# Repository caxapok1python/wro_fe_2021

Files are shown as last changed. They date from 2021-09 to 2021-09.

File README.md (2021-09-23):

# World Robotic Olympiad 2021 Future Engineers

## Our YouTube Video
    https://youtu.be/UyoNl7fKj5E

## Introduction

The pandemic has accelerated the introduction of digital technologies in all spheres of life. 41% of company executives from 45 countries are preparing to work in a new post-crisis reality, investing in accelerating business automation.

Sustainable development of companies even before the pandemic was associated with digital technologies. Automation of transport gives many advantages, but it is also important that the introduction of machine labour reduces risks. Some of them are shortages of workers, low attractiveness of labour in the industry. These circumstances necessitate the use of labour-saving technologies: digital, intellectual and robotic. Basically, these technologies are represented by robotics, one of the most important functions of which is intellectual, it is to quickly obtain information, data on processes performed and products to improve the efficiency of decision-making and implementation of management decisions in autonomous movement. When introducing robotics in logistics organisations, it is necessary to take into account the regional characteristics and specifics of specific sectors of transportation. Regional features of robotics may be related to the peculiarities of the region's development. These features include the level and conditions of socio-economic development of the region, infrastructure development, demographic trends, competitiveness of the transport sector to attract labour in comparison with other industries, etc. Industry features that require robotisation may be related to the need to perform monotonous repetitive processes, the presence of heavy, dangerous and harmful activities. An important condition for robotisation of processes in the field of transportation is the possibility of compiling certain algorithms that underlie the functioning of robotics.

##### Based on the above facts, the following tasks of robotics in the field of transportation can be distinguished:

- Monitoring and forecasting;

- Reducing the cost of transportation;

- Improving logistics security;

- Solving personnel problems;

- Reducing the costs of employees' bad faith;

- Expanding the possibilities of using equipment - robots can be all-weather and work at any time of the day.

``Kinematic scheme``

``Calculation part``

>3.1 Engine calculation
    
1) Motor torque is the force with which it acts on the rotating axle. In order for the robot to move, it is necessary that this force exceeds the weight of the robot (expressed in N/m).

When travelling in a straight line at a distance of 1 m, calculate the acceleration required to achieve a speed of 1 m/s.

    V^2 = v_0^2+2ad

Where is the distance travelled by the robot - its initial speed (start from the place, so ),

    A = (v^2-v_0^2)/2d

Where is the speed of the robot, its acceleration.

Substitute the values adopted in our model, we'll get

    A = (1^2-0)/2=0.5 m/c^2 - acceleration required to achieve a speed of 1 m/s

The torque that is necessary to move the robot and obtain the acceleration necessary to achieve maximum speed is calculated as follows:

When - moment of inertia and - angular acceleration, we get

    M = mrag/2=(8*9.8*0.13*10)/2=51 
        (mN*m)=0.52 (kg*cm)

Here m/s2 - acceleration of free fall (round it to 10), - radius of the wheel, - mass of the entire robot

To convert the value expressed in Nm to kg·cm, it should be taken into account that 1H = 0.102 kg and 1m = 100 cm. Therefore, 50 mN·m = 50 · 0.102 : 1000 * 100 = 0.51 kg · cm.

2) To calculate the maximum power of the engines, we will need a speed that is expressed in revolutions per minute

#####
    V=60ω/2πr (rpm)
#####
    V=(60*1)/(2π*0.13)=73.46 (rpm)

Motor power is proportional to torque and speed, substituting formulas for torque and frequency, we get:

    P=M*v=(8*9.8*0.13*0.5)/(2*0.13)=19.6 (W)

We got the total power for all engines, in our case the engines are two, so we need to divide the result by two.

For our two-wheeled robot, using a gear ratio equal to 10, the characteristics of the installed engines should be as follows:

**Speed** - 2000 rpm.

**Torque** - 60 mN*m

**Electric power** - 50 W

>3.2 Servo drive calculation

The robot on the turn of the front axle uses micro servo 9g sg 90 servo drives.

The torque on the shaft of this drive is 1.6 kg cm.

The maximum load of the inverted wheel is 1-1.3 kg.

When the servo drive is located on the axis of rotation of the swivel fist with a stop of the drive nozzle to the upper fist, we create a moment of force that allows you to keep the wheel in the required angle.

    M=[r *F ]

Where is M torque?

    F - power
    R - radius

Using this formula, we can find the power that the servo drive can withstand.

Given:

    M=1.6 (kg*cm) = 0.16 (H*m)
#####
    R=0.025( m)
#####
    F=M/r=0.16/0.025=6.4 (H)

Conclusion: Such power is enough for our task, as the servo acts through the lever, not directly.

>3.3 Screw calculation

-   Information system.

>>4.1 Electronic components 
>####4.1.1 selection of engine control driver.
>Dual L298N driver - made on the basis of the L298N chip with low internal resistance, PWM control capability and output current up to 5 A, which is a suitable solution for a project with high current consumption. The L298N driver is compatible with the entire Arduino line as well as with any other microcontrollers.

**Characteristics:**

- logic voltage 5 Volts;

- engine operating voltage from 7.2 to 20 Volts DC;

- operating output current to the channel up to 68A (start mode);

**Size:** 4.5*4.1 cm.

The motor paired driver works debugged, as the operating current is enough for the motor, which at its peak consumes 2A at 12V.

>4.1.2 Battery calculation

**Single battery:**

Formulas that determine the relationship between the current that the battery gives to the load, its capacity and the relative discharge rate:

    I_bat = C_rate*C_bat
#####
    I_bat - current in amperes given to the load by one battery;
    
**C_bat** - nominal battery capacity in ampere hours (means the product of amperes per watch), which is usually labelled on the battery;

C_rate is the relative discharge rate of the battery, defined as the discharge current divided by the theoretical current that the battery can give out within one hour and its capacity will be fully consumed.

**I_bat** = 30 A;

**C_bat** = 3000 mAh;

Where does **C_rate** = 10 seconds come from;

Operating time t and relative discharge rate of the C_rate battery are bound by an inverse proportional dependence:

    t=1/C_rate

Let's note that this is a theoretical time of work. Due to a variety of external factors, real operating time will be about 30% less than calculated according to this formula. It should also be noted that the permissible discharge depth of the battery further limits its operating time.

The watt-hour energy stored in the battery is calculated by the formula:

    E_bat=V_bat C_bat^

**Here:**

**E_bat** - nominal energy stored in the battery in watt hours,

**V_bat** - rated battery voltage in volts

**C_bat** - nominal battery capacity in ampere hours (Ah)

**V_bat** = 4.2 B;

**E_bat** = 12.6 Wh;

The energy in joules (watt seconds, Wt-s) is calculated by the formula

    E_(bat,joul) = 3600*E_(bat,Wh);
#####
    E_(bat,joul) = 45.36 kJ;

It is known that at a current of one ampere, a charge of one pendant passes through the cross section of the conductor in one second. Therefore, the battery charge is determined from the expression Q = I · t, taking into account the known battery capacity in ampere hours, which determines the current given by the battery to the load for 3600 seconds:

    Q_bat = 3600<OPUS-CC>*C_BAT_

**Q_bat** - battery charge in pendants (K)

Cbat is the nominal capacity of the battery in ampere hours.

**Q_bat** = 108 kCl;

**Battery pack**

The rated voltage of the battery pack in volts is determined by the formula:

V_bank=V_bat*N_s

**Here:**

**Vbat** - rated voltage of the battery in volts,

**Vbank** - rated voltage of the battery pack in volts

**Ns** - number of batteries in one of several groups of serially connected batteries;

**Ns** = 4 pcs.

**Vbank** = 16.8 V;

Battery capacity in ampere hours, **Cbank** is determined by the formula:

    C_bank=C_bat*N_p

**C_bank** = 12 Ah;

The nominal energy in Ebank watt hours stored in the battery pack is determined by the formula:

    E_bank = E_bat *N_p*N_s_

**Np** - the number of groups of serially connected batteries connected in parallel

**Np** = 4 pcs.

**E_bank** = 201.6 Wh

Joule energy is calculated by the formula:

    E_(bank,joul) = 3600*E_(bank,Wh)

Here Ebank, Wh is the nominal energy of the battery pack in watt hours.

    E_(bank,joul) = 725.76 kJ;

The charge in the pendants of the Qbank battery pack is defined as the sum of the charges of all batteries in the unit:

    Q_bank = Q_bat*N_p *N_s

**Q_bank**=1 728 kCl

The discharge current of the Ibank battery pack is calculated by the formula:

    I_bank = I_bat*N_p

**I_bank** = 120 A

The operating time of the tbank battery pack is determined by the formula:

    T_bank = t_bat *N_p

**T_bank** = 24 min.

4s2p battery assembled on 18650 high-current batteries. The choice was made on these batteries, as they have large capacity, low self-discharge, light and easy to maintain, and have a long cycle life.

Assembly of 8 high-current batteries, capacity of each 3000 mAh, assembly will be in 4S2P format (two 4 can batteries in parallel), which is supposed to give a total capacity of 12 Ah.

>4.2 Software algorithms

First of all, the software algorithm of the car is based on its mechanical structure.

**Software design:**

1. Reading the competition regulations

2. Finding permanent points in the image. In our case, I considered the sides a permanent point, as they are always black and are always in the area of operation of the camera.

3. Choosing a way to track signs. I decided to find the image mask according to the desired colour, find the outline and determine the middle of the sign.

4. Turn tracking algorithm. It's In this aspect, I was guided by field elements that can be seen at each new turn - colour lines. I cut out the mask in the same way and find the middle.

5. Harmonisation of the software and mechanical device of our car.

First of all, I read the regulations of the competition. Next, for the constant movement of the car, you need to choose beacons on which we can move during the attempt. It is also worth taking care of the detour of the signs by tracking them in the image. And I also solved the problem of counting the turns taken, counting the turning lanes. After writing the detailed code, I had to agree on the basic controls of the vehicle. This was realised in the precise rotation of the servo control of the front axle of the machine.

>4.2.1 schematic diagram
>https://github.com/caxapok1python/wro_fe_2021/blob/main/Schematic.pdf

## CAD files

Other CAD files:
3D Models.dwg

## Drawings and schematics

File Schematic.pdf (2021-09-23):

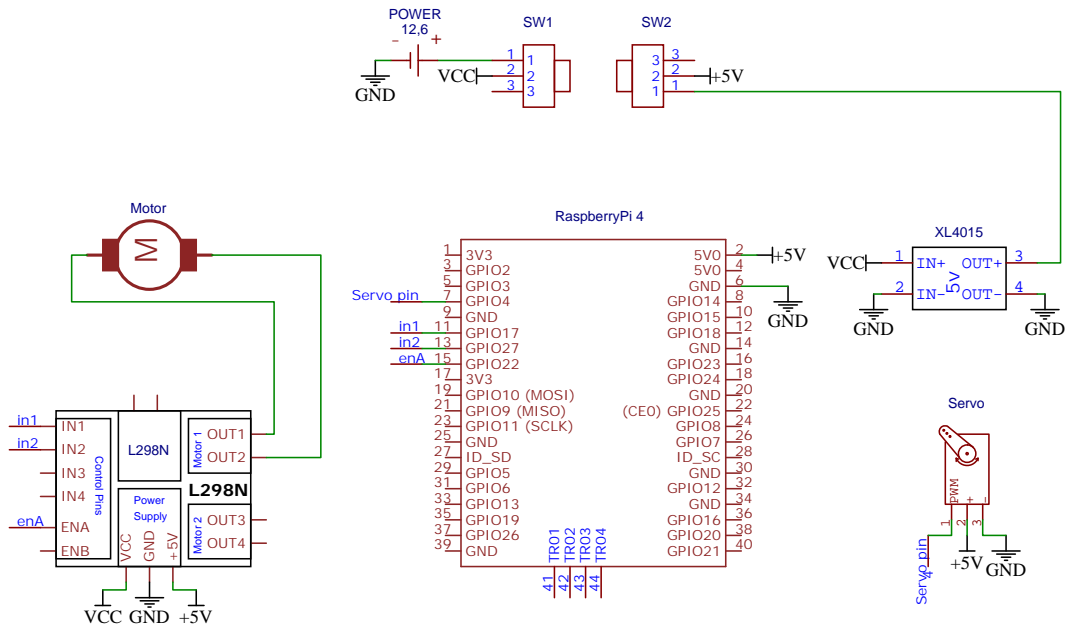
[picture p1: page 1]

Drawn By: Орехов Иван

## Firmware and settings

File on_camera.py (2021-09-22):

# imports
import cv2
import numpy as np
import RPi.GPIO as GPIO
import time
import inspect


GREEN = ((70, 107, 0), (93, 255, 255))
RED = ((129, 59, 6), (255, 255, 255))
BOARD = ((0, 0, 0), (255, 127, 74))
YELLOW = ((0, 87, 95), (25, 155, 145))
BLUE = ((112, 19, 68), (121, 255, 137))

def is_in(rng, value):
    if min(rng) <= value <= max(rng):
        return True
    return False

class Drive:
    forward = (True, False)
    backward = (False, True)


class Motor:
    def __init__(self, in1=27, in2=22, pwm=17):
        self.in1 = in1
        self.in2 = in2
        self.pwm = pwm

        # настраиваем порты
        self.setup_pins()
        self.pwr = GPIO.PWM(self.pwm, 1000)
        self.pwr.start(0)

    def setup_pins(self):
        GPIO.setup(self.in1, GPIO.OUT)
        GPIO.setup(self.in2, GPIO.OUT)
        GPIO.setup(self.pwm, GPIO.OUT)

    def drive(self, direction, speed):
        GPIO.output(self.in1, direction[0])
        GPIO.output(self.in2, direction[1])
        self.pwr.ChangeDutyCycle(speed)


class Servo:
    def __init__(self, pin=4, rng=()):
        self.pin = pin
        self.minimum, self.maximum = rng

        # настраиваем порты
        self.setup_pins()
        self.servo1 = GPIO.PWM(self.pin, 50)
        self.servo1.start(0)
        self.calc_flip()
        
    def calc_flip(self):
        k = self.maximum - self.minimum
        self.center = int(int(((k / 2) + self.minimum)) - k/2/4)
        self.full_left = self.minimum
        self.half_left = int(self.center-10)
        self.full_right = self.maximum
        self.half_right = int(self.center + k/2/4)
        
    def calc(self):
        k = self.maximum - self.minimum
        self.center = int(((k / 2) + self.minimum))
        self.full_left = self.minimum
        self.half_left = int(self.center - k/2/4)
        self.full_right = self.maximum
        self.half_right = int(self.center + k/2/4)

    def setup_pins(self):
        GPIO.setup(self.pin, GPIO.OUT)

    def angle(self, angle):
        duty = angle / 18 + 2
        angle = angle / 10
        self.servo1.ChangeDutyCycle(angle)
        self.servo1.ChangeDutyCycle(angle)


class Camera:
    def __init__(self, cam: int):
        self.cam = cv2.VideoCapture(cam)

    def capture_img(self):
        _, frame = self.cam.read()
        return frame

    def crop(self, frame, x, y):
        return frame[y[0]:y[1], x[0]:x[1]]

    def to_hsv(self, frame):
        return cv2.cvtColor(frame, cv2.COLOR_BGR2HSV)

    def show(self, mask=None, name=None):
        if name:
            cv2.imshow(name, mask)
        else:
            cv2.imshow('xxx', mask)

    def mask(self, hsv_image, range):
        start, stop = range
        return cv2.inRange(hsv_image, start, stop)

    def moment(self, mask):
        moments = cv2.moments(mask, 1)
        m01 = moments['m01']
        m10 = moments['m10']
        area = moments['m00']
        return m01, m10, area

    def center(self, moment):
        return int(moment[1] / moment[2])

    def line(self, frame, color: tuple, thickness: int, x=0, y=0):
        if x:
            cv2.line(frame, (x, 0), (x, 210), color, thickness)
        if y:
            cv2.line(frame, (0, y), (640, y), color, thickness)
        return 0

    def point(self, frame, center, color=(255, 255, 255), radius=1):
        cv2.circle(frame, center, radius=1, color=color, thickness=-1)

    def draw_box(self, frame, mask, min_range, max_range, draw=True, color=()):
        if self.moment(mask)[2] >= min_range:
            contours0, hierarchy = cv2.findContours(mask.copy(), cv2.RETR_TREE, cv2.CHAIN_APPROX_SIMPLE)
            center = ()
            # перебираем все найденные контуры в цикле
            for cnt in contours0:
                ar = cv2.contourArea(cnt)
                # print(ar)
                if ar >= max_range:
                    rect = cv2.minAreaRect(cnt)  # пытаемся вписать прямоугольник
                    if rect[0][1] > 0:
                        center = tuple(rect[0])
                        if draw:
                            box = cv2.boxPoints(rect)  # поиск четырех вершин прямоугольника
                            box = np.int0(box)  # округление координат
                            cv2.drawContours(frame, [box], 0, color, 2)  # рисуем прямоугольник
                    return center, ar

    def stop(self):
        self.cam.release()
        cv2.destroyAllWindows()


class AI(Camera):  # класс автопилота
    def bricks(self, frame, hsv, min_area=1000, max_area=1500, draw_box=(True, True), draw_lines=(True, True)):
        global RED, GREEN
        # red
        mask = self.mask(hsv, RED)

        red = self.draw_box(frame, mask, min_area, max_area, draw=draw_box[0], color=(0, 0, 255))
        # print(red)
        if red:
            red_center, red_area = red
            if red_center and draw_lines[0]:
                self.line(frame, (0, 0, 255), 1, x=red_center[0], y=red_center[1])  # рисуем линии по центру
        # green
        mask = self.mask(hsv, GREEN)
        green = self.draw_box(frame, mask, min_area, max_area, draw=draw_box[1], color=(0, 255, 0))  # рисуем коробку кубика
        if green:
            green_center, green_area = green
            if green_center and draw_lines[1]:
                self.line(frame, (0, 255, 0), 1, x=green_center[0], y=green_center[1])  # рисуем линии по центру
        return red, green

    def create_cursor(self, frame, centers: tuple):
        global correct
        if centers:
            #print('centers=', centers)
            if centers[0] and not centers[1]:
                # green
                if centers[0]:
                    curse = centers[0][0][0] - correct
                    self.line(frame, (0, 255, 0), 2, x=curse)  # рисуем линию курса
                    return curse
            elif centers[1] and not centers[0]:
                # red
                if centers[1]:
                    curse = centers[1][0][0] + correct
                    self.line(frame, (0, 0, 255), 2, x=curse)  # рисуем линию курса
                    return curse
            elif centers[1] and centers[0]:
                return False
            elif not centers[1] and not centers[0]:
                return False

    def lines(self, frame, hsv, min_area=200, max_area=200, draw_box=(True, True), draw_lines=(True, True)):
        global YELLOW, BLUE
        # blue
        mask = self.mask(hsv, BLUE)
        blue = self.draw_box(frame, mask, min_area, max_area, draw=draw_box[0], color=(255, 20, 20))
        if blue:
            blue_center, blue_area = blue
            if blue_center and draw_lines[0]:
                self.line(frame, (255, 20, 20), 1, x=blue_center[0], y=blue_center[1])  # рисуем линии по центру
        # yellow
        mask = self.mask(hsv, YELLOW)
        yellow = self.draw_box(frame, mask, min_area, max_area, draw=draw_box[1], color=(20, 255, 255))
        if yellow:
            yellow_center, yellow_area = yellow
            if yellow_center and draw_lines[1]:
                self.line(frame, (255, 20, 20), 1, x=yellow_center[0], y=yellow_center[1])  # рисуем линии по центру
        return blue, yellow

    def borders(self, frame, hsv, min_area=1000, max_area=1500, draw_points=True, color=(255, 255, 255)):
        global BOARD, zones
        mask = self.mask(hsv, BOARD)
        left_zone = self.crop(mask, (0, zones), (0, 480))
        left = self.draw_box(frame, left_zone, min_area, max_area, draw=False)
        if left:
            left_center, left_area = left
            if left_center and draw_points:
                self.point(frame, left_center, color, 5)
        center_zone = self.crop(mask, (zones, 640 - zones), (0, 350))
        center = self.draw_box(frame, center_zone, min_area, max_area, draw=False)
        if center:
            center_center, center_area = center
            if center_center and draw_points:
                x, y = center_center
                x += zones
                center_center = x, y
                self.point(frame, center_center, color, 5)
        right_zone = self.crop(mask, (640 - zones, 640), (0, 210))
        right = self.draw_box(frame, right_zone, min_area, max_area, draw=False)
        if right:
            right_center, right_area = right
            if right_center and draw_points:
                x, y = right_center
                x += 640-zones
                right_center = x, y
                self.point(frame, right_center, color, 5)
        return left, center, right


class AutoPilot(AI, Motor, Drive, Servo):
    def avoid_borders(self, current_areas, half_correct=7, board_correct=13000, speed=90):
        global correction_speed
        if current_areas:
            left, _, right = current_areas
            if left and right:
                if left[1] and right[1]:
                    if left[1] - right[1] > board_correct:
                        driver.drive(dir.forward, speed)
                        servo.angle(servo.half_right+half_correct)
                        return 1
                    elif left[1] - right[1] < -board_correct:
                        servo.angle(servo.half_left-half_correct)
                        return -1
            return 0

    def rotate(self, speed):
        func = inspect.stack()[1].function
        if 'clockwise' in func:
            driver.drive(dir.forward, speed)
            servo.angle(servo.full_right+5)
            return 1
        elif 'counterclockwise' in func:
            servo.angle(servo.full_left-5)
            return 1
        return 0

    def park(self):
        global speed
        speed = 0

    def clockwise_qual(self, speed=100, rot_speed=85, cor_speed=0):
        rotates = 0
        rotate_logic = [False, False]
        start_time = time.time()
        while True:
            frame = self.capture_img()
            cropped = self.crop(frame, (0, 640), (60, 210+60))
            hsv = self.to_hsv(cropped)
            blue, yellow = self.lines(cropped, hsv, draw_lines=(False, False), draw_box=(False, False))
            # print('colors=', blue, yellow)
            board = self.borders(cropped, hsv, draw_points=False)
            # ssprint('board=', board)
            bort = self.avoid_borders(board, 7, 13000, speed-cor_speed)
            # print(bort)
            if not bort:
                if board[1]:
                    if board[1][1] > 9000:
                        self.rotate(rot_speed)
                    else:
                        servo.angle(servo.center)
                        driver.drive(dir.forward, speed)
            if yellow:
                if len(yellow) and len(yellow[0]) and yellow[0][1] > 100:
                    rotate_logic[0] = True
            if blue:
                if len(blue) and len(blue[0]) and blue[0][1] > 100:
                    rotate_logic[1] = True

            if rotate_logic == [True, True]:
                rotates += 1
                rotate_logic = [False, False]
            # print(rotates)
            if rotates == 12:
                print(print("--- %s seconds ---" % (time.time() - start_time)))
                start_time = time.time()
                rotates = 0
                break
        self.park()

    def clockwise_final(self, speed=100, rot_speed=85, cor_speed=0, cor_angle=7):
        rotates = 0
        rotate_logic = [False, False]
        start_time = time.time()
        fps_start = start_time
        fps = 0
        while True:
            frame = self.capture_img()
            cropped = self.crop(frame, (0, 640), (60, 210 + 60))
            hsv = self.to_hsv(cropped)
            blue, yellow = self.lines(cropped, hsv, draw_lines=(False, False), draw_box=(False, False))
            # print('colors=', blue, yellow)
            board = self.borders(cropped, hsv, draw_points=False)
            # print('board=', board)
            bort = self.avoid_borders(board, 7, 10000, speed - cor_speed)
            # print(bort)
            red, green = self.bricks(cropped, hsv, draw_lines=(False, False), draw_box=(False, False), max_area=3000)
            cursor = self.create_cursor(frame, (red, green))
            if cursor:
                if is_in((zones, 640-zones), cursor):
                    driver.drive(dir.forward, speed)
                    servo.angle(servo.center)
                elif is_in((-1000, 0), cursor):
                    driver.drive(dir.forward, speed-15)
                    servo.angle(servo.full_right)
                elif is_in((0, zones//2), cursor):
                    driver.drive(dir.forward, speed-15)
                    servo.angle(servo.half_right+cor_angle)
                elif is_in((zones//2, zones), cursor):
                    driver.drive(dir.forward, speed-15)
                    servo.angle(servo.half_right)
                elif is_in((640-zones, 640-zones+zones//2), cursor):
                    driver.drive(dir.forward, speed-15)
                    servo.angle(servo.half_left)
                elif is_in((640-zones, 640), cursor):
                    driver.drive(dir.forward, speed-15)
                    servo.angle(servo.half_left-cor_angle)
                elif is_in((640, 2000), cursor):
                    driver.drive(dir.forward, speed-15)
                    servo.angle(servo.full_left)

            elif not bort:
                if board[1]:
                    if board[1][1] > 9000:
                        self.rotate(rot_speed)
                    else:
                        servo.angle(servo.center)
                        driver.drive(dir.forward, speed)
            if yellow:
                if len(yellow) and len(yellow[0]) and yellow[0][1] > 150:
                    rotate_logic[0] = True
            if blue:
                if len(blue) and len(blue[0]) and blue[0][1] > 180:
                    rotate_logic[1] = True

            if rotate_logic == [True, True]:
                rotates += 1
                rotate_logic = [False, False]
            # print(rotates)
            if rotates == 12:
                print("--- %s seconds ---" % (time.time() - start_time))
                start_time = time.time()
                rotates = 0
            fps += 1
            if time.time() - fps_start >= 1:
                print(fps)
                fps = 0
                fps_start = time.time()

        #self.park()

    def test(self):
        while True:
            frame = ap.capture_img()
            cropped = ap.crop(frame, (0, 640), (60, 210 + 60))
            hsv = ap.to_hsv(cropped)

            print(ap.bricks(cropped, hsv))
            print(ap.borders(cropped, hsv))
            print(ap.lines(cropped, hsv, 50, 100))
            ap.show(cropped)
            key = cv2.waitKey(1) & 0xFF
            if key == ord('q'):
                break


if __name__ == '__main__':
    cam_num = 0
    ap = AutoPilot(cam_num)

    GPIO.setmode(GPIO.BCM)
    servo = Servo(rng=(65, 120))
    dir = Drive()
    driver = Motor()

    speed = int(input('speed #> '))
    correction_speed = speed - 10 if speed > 70 else speed
    rotate_speed = speed-15 if speed > 70 else speed
    zones = 250
    correct = 300

    # запоминаем стартовые параметры
    frame = ap.capture_img()
    start_bricks = ap.bricks(frame, ap.to_hsv(frame), draw_box=(False, False), draw_lines=(False, False))
    start_boards = ap.borders(frame, ap.to_hsv(frame), draw_points=False)

    # road zone
    #ap.clockwise_final(speed=speed, rot_speed=rotate_speed, cor_speed=correction_speed)
    ap.test()
    # parking
    ap.stop()

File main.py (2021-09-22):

from wiringpi import *

wiringPiSetupGpio()

def pwr(proc: int):
    return int((255*proc) / 100)


def inRange(rang, val):
    start, stop = rang
    return start <= val <= stop


class Motor:
    def __init__(self, conf):
        self.IN_A, self.IN_B, self.PWR = conf

        self.setup_pins()

    def setup_pins(self):
        pinMode(self.IN_A, GPIO.PWM_OUTPUT)
        pinMode(self.IN_B, GPIO.PWM_OUTPUT)
        pinMode(self.PWR, GPIO.PWM_OUTPUT)

    def forward(self, power: int):
        pass


class HCSR04:
    def __init__(self, trig, echo):
        self.trig = trig
        self.echo = echo

    def setup(self):
        pinMode(self.trig, GPIO.PWM_OUTPUT)
        pinMode(self.echo, GPIO.PWM_INPUT)

    def get_dist(self):

        digitalWrite(sel.trig, 0)
        delayMicroseconds(5)
        digitalWrite(self.trig, 1)


        delayMicroseconds(10)
        digitalWrite(self.trig, 0)

        duration = pulseIn(self.echo, 1)

        dist = (duration / 2) / 29.1
        return int(dist)

class Servo:
    def __init__(self, pin):
        self.logic = pin
        self.max_angle = 180
        self.center = 60

    def angle_to_shim(self, angle):
        return (255 * angle) / self.max_angle

    def setup(self):
        pinMode(self.logic, GPIO.PWM_OUTPUT)
        pwmWrite(self.logic, self.angle_to_shim(self.center))

    def angle(self, angle):
        pwmWrite(self.logic, self.angle_to_shim(angle))


class AI:
    def __init__(self):
        self.stright = (220, 430)
        self.conditions()

    def conditions(self):
        road = ((60, 150), (0, 70), (0, 70))
        rotate = ((0, 60), (70, 300), (70, 300))
        out = ((150, 300), (70, 300), (70, 300))
        self.pos = (out, road, rotate)

    def sonic_range(self, sonic, position, mode):
        out = False
        if mode == 'front':
            if inRange(position[0], sonic[0]):
                out = True
        elif mode == 'left':
            if inRange(position[1], sonic[1]):
                out = True
        elif mode == 'right':
            if inRange(position[2], sonic[2]):
                out = True
        return out

    def on_road(self, cam):
        ax = (cam[-2], cam[-1])
        for i in range(2):
            if inRange(self.stright, ax[i]):
                return True
        return False


    def detect_zone(self, sonic, cam):
        # cam = (red, green, red_x, green_x)
        # sonic = (front, left, right)
        positions = ('out', 'road', 'rotate')
        current = positions[0]
        for position in range(3):
            if position == 1 and not self.on_road(cam):
                if self.sonic_range(sonic, self.pos[position][0], 'front'):
                    current = positions[position]
        return current

    def line(self, zone, sonic):
        lines = ('left', 'center', 'right')
        # if zone == 'road':
        #     for i in range(3):
        #         if self.sonic_range(sonic)


def setup_controls():
    global servo, front, left, right
    servo.setup()
    front.setup()
    left.setup()
    right.setup()





def main():
    servo = Servo(pin=14)
    front = HCSR04(trig=17, echo=27)
    left = HCSR04(trig=23, echo=24)
    right = HCSR04(trig=20, echo=21)
    setup_controls()
    while True:
        f_cm = front.get_dist()
        l_cm = left.get_dist()
        r_cm = right.get_dist()
        print(":".join(map(str, (f_cm, l_cm, r_cm))))



if __name__ == '__main__':
